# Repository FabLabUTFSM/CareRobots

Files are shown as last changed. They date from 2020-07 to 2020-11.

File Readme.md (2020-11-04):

# CareRobots

<p align="center">
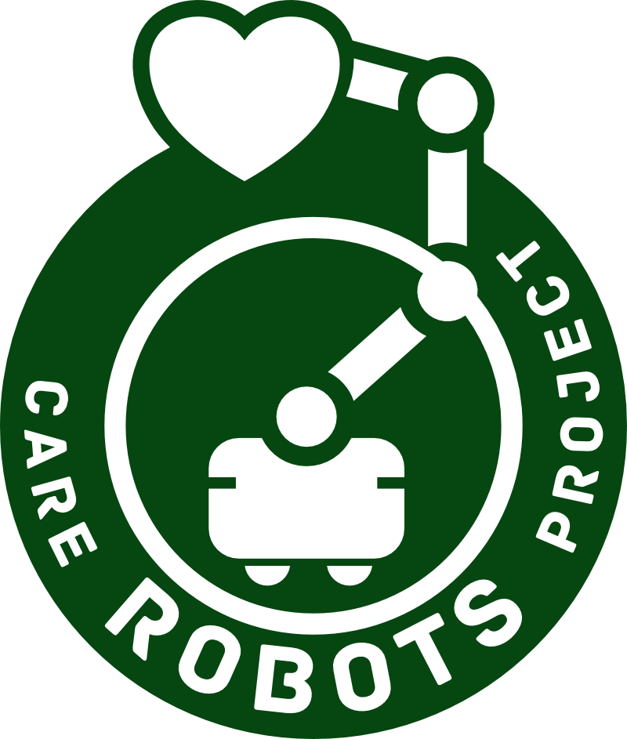
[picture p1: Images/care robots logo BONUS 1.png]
  
</p>

CareRobots is an OpenSoruce project developed by [Fab Lab UTFSM](http://fablab.usm.cl/), [LightHouse-DIG](https://lighthouse-dig.com/), [Center for Engineering Education and Outreach](https://ceeo.tufts.edu/) and [Soko Tech](https://soko.tech/). 

We aim to build low cost telepresence robots, that can be build in any Fab Lab/Makerspace around the world, this robot are intented to protect healthcare service personnel from the COVID-19 spread from infected patients. 

## Firmware

1.0: This firmware is built for an [Adafruit Huzzah feather ESP32](https://learn.adafruit.com/adafruit-huzzah32-esp32-feather/overview), currently other boards aren't working with such reliability.

### Schematic

<p align="center">
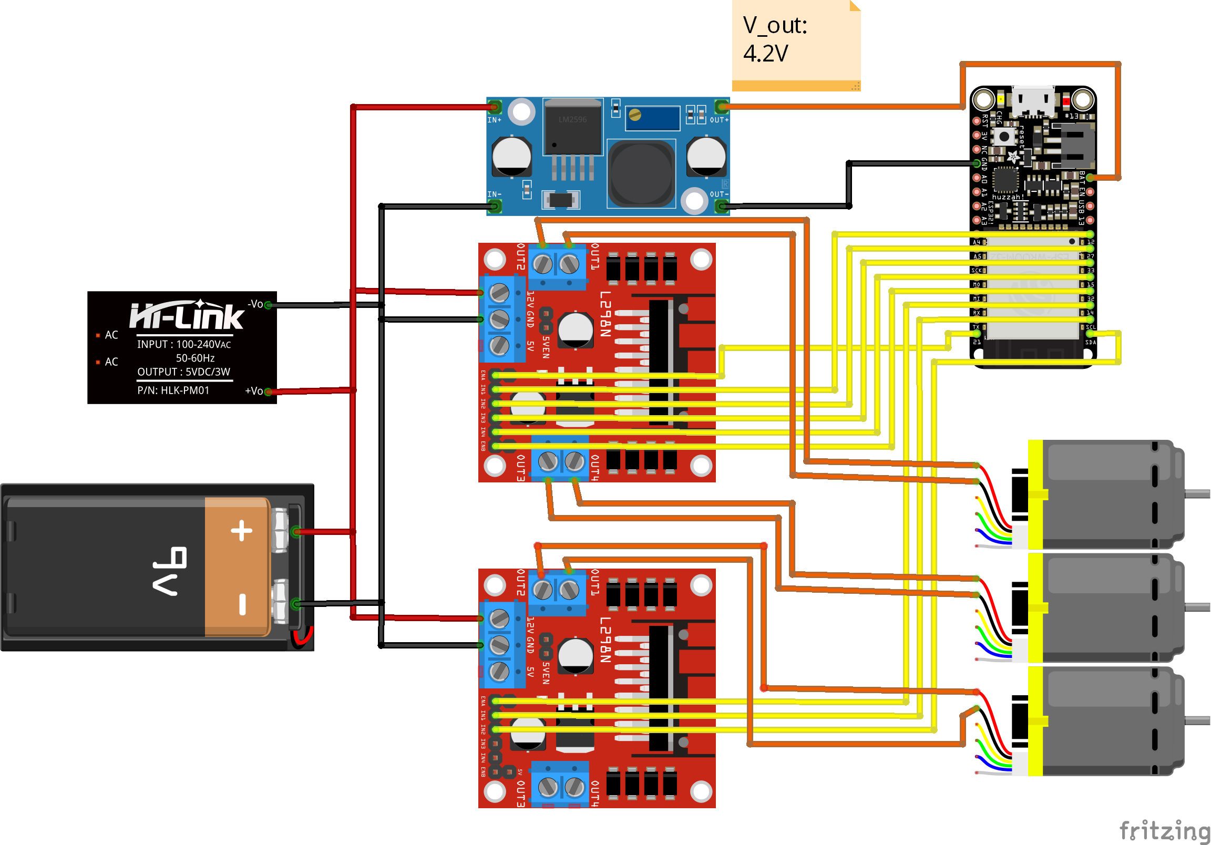
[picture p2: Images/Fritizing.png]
  
</p>

### Libraries

If you are downloading the softwares directlly you hace to coinsider that they are coded using [Platformio](https://platformio.org/), if you are using the Arduino IDE, you will find the codes in the src folder, they will titled as main.cpp (if you fill is more comftable, you can change the extension to .ino), and download the following libraries: 

#### ESP32 - Bluetooth
- [BluetoothSerial](https://github.com/espressif/arduino-esp32/tree/master/libraries/BluetoothSerial)

#### ESP32 - WiFi
- [WebServer](https://github.com/espressif/arduino-esp32/tree/master/libraries/WebServer)
- [analogWrite](https://github.com/ERROPiX/ESP32_AnalogWrite)

#### ESP8266 - WiFi
- [ESP8266WiFi](https://github.com/esp8266/Arduino/tree/master/libraries/ESP8266WiFi)
- [ESP8266WebServer](https://github.com/esp8266/Arduino/tree/master/libraries/ESP8266WebServer)

### Configuration

The current code we have been using is Wifi_ServerClient_ESP32. Key configurations: 

#### WiFi

Set your WiFi passports, to connect the board to your home network.  
```
bool wifiPass = false ; //True if the WiFi network has password; False if not. 
const char* ssid = ""; //WiFi ssid
const char* password = ""; //WiFi password
```

#### Motor Settings

##### Conections

This variables configure the motors pins. In this case, the conection are configured for the conections showed in [Schematic](#Schematic) section. 

```

const int pinMotor[]= {12,27,15,33,22,23};// {moto1CW,motor1CCW,moto2CW,motor2CCW,moto3CW,motor3CCW}
const int pinEnable[]={21,32,14};
const int led = 13;
 ```
##### Torque Ramp Setting

This section works specifically for the torque ramp variables. The torque ramp is used as a patch meanwhile an speed control PID is implemented. 

Key:
* enableTorqueRamp: True if the user is going to work with a torque ramp, false if the user is going to use fix torque value, set in motorSpeed. 
 * maxPayload: PWM payload in wich the robot breaks the inertia. The maximum value it can take is 255. 
 * minPayload: PWM payload for the normal speed we want to aim for our robot. 
 * torqueRampSmoother: Will set te amount of cycles in wich the robot will reach the desired speed. A big number will take more time to reach the speed, but in a smoother way. 
 * delay: Time wich a PWM torque stays working. 
 The ramp time will be defines by the following equation: (maxPayload-minPayload)*delay/toqueRampSmoother. 

```
bool enableTorqueRamp = true;
const int maxPayload = 255;
const int minPayload = 240;
const int torqueRampSmoother =10; 
const int torqueRampDelay= 100; 
const int motorSpeed = 255;
```
##### Motor direction

This variables are designed to control the motor direction from the code and not from the conections. In case a motor is conected in an oposite direction to the shown in the schematics. The user just have to change the variable value for that motor, and it wheel automatically change direction. 

```
bool motor1 = false;
bool motor2 = true;
bool motor3 = false;
```

### Install NodeMCU in Arduino IDE

To install the NodeMCU in the Arduino IDE, you can follow the following [instructions](https://www.instructables.com/id/Quick-Start-to-Nodemcu-ESP8266-on-Arduino-IDE/). 

## Structure

<p align="center">
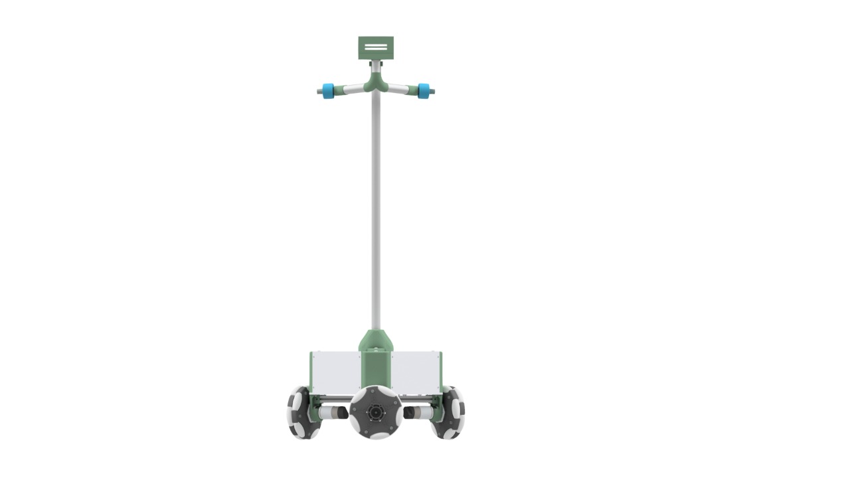
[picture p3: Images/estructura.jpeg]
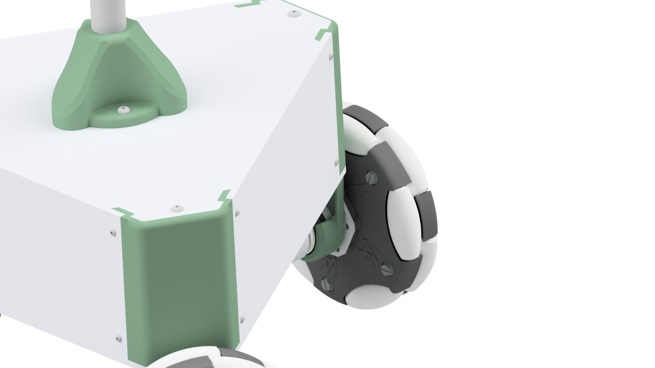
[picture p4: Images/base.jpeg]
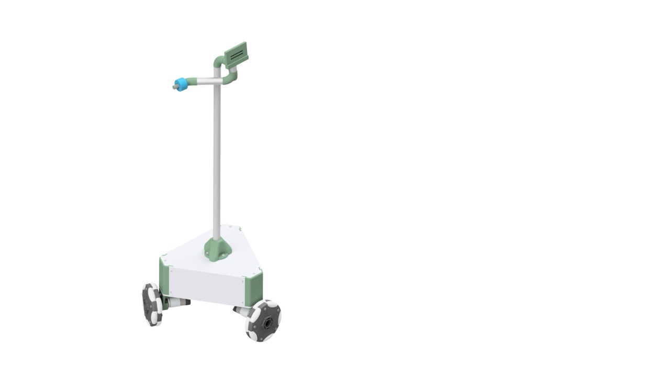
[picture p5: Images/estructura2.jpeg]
   
</p>

## Fabrication 

In order to make CareRobots easy to fabricate in any Fab Lab/Makerspace in the world, we only use 3D printers and laser cutters, all parts can be downloaded in the following [link](https://drive.google.com/drive/folders/1tkrLoz_K_6apnlru4AjxvQd69-fxhUXf?usp=sharing).

### 3D Printed - Structure

|Part Name |Number of parts |  Download Link |
| :-: | :-: |  :-: |
|  B1 | 1  |  [link](https://drive.google.com/file/d/1X95zLryoru4crX6b115vtqp_EDh8kSQb/view?usp=sharing)|
|  B2 | 2  |  [link](https://drive.google.com/file/d/1_fum_8d5C-oLnXPcYOniwOqLqxyNqtJm/view?usp=sharing) |  
|  B3 | 1  |  [link](https://drive.google.com/file/d/1nL7G1LNKwou2jkkLmy965ZC8Md9wTHIw/view?usp=sharing) |
|  Bat | 1  |  [link](https://drive.google.com/file/d/17oT4-NMZ_uCZ2WhJEKf6BcBfo7XZ6th5/view?usp=sharing) |
|  L_v2 | 3  |  [link](https://drive.google.com/file/d/1hJeNZyvru78oPO08zw2eOO0yUmgKt_Df/view?usp=sharing) |
|  M | 3  |  [link](https://drive.google.com/file/d/12ri8eZTseVjtSSoXTZQLDR91Xk1uGaeo/view?usp=sharing) |

### Laser Cutted - Structure

|Part Name |Number of parts | Format |  Download Link |
| :-: | :-: |  :-: | :-: |
| A1  |1 | .dxf |  [link](https://drive.google.com/file/d/1qUMhkHjF6LQkufdu41Rsg2A58V7bNPKg/view?usp=sharing) |
| A1  |1 | .pdf |  [link](https://drive.google.com/file/d/10A2T8DMf_OYUFBTCkRg2jiaPDkv-Y5n-/view?usp=sharing) |
| A2  |1 | .dxf |  [link](https://drive.google.com/file/d/1UI6lDsppqcmhL-nH30FwWpygrrH0wOEs/view?usp=sharing) |
| A2  |1 | .pdf |  [link](https://drive.google.com/file/d/1junfC2UCxdz8u_q4p5oR-OMI-dwqzFFS/view?usp=sharing) |
| A3  |3 | .dxf |  [link](https://drive.google.com/file/d/1FhoujUBVxT0hbg1iW205K-4B8KdyHQ2V/view?usp=sharing) |
| A3  |3 | .pdf |  [link](https://drive.google.com/file/d/18cWZgs_5W19GRg0fgFSUVpIVmK2tZZqf/view?usp=sharing) |

### 3D Printed - Gimbal

__Do not build right away, the structure is being tested in Fab Lab UTFSM, uptdates will be posted__

<p align="center">
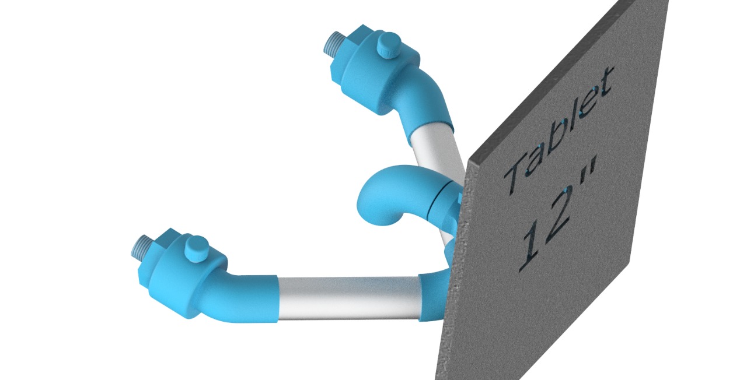
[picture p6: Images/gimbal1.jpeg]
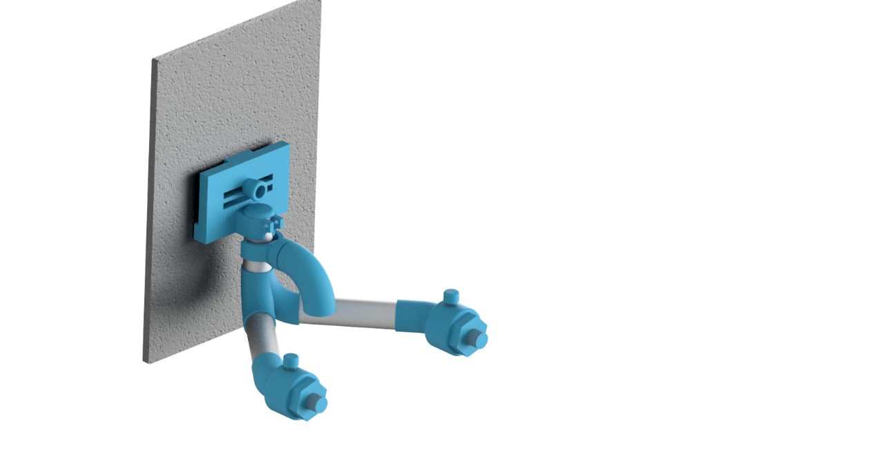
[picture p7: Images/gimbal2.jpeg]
 
</p>

|Part Name |Number of parts | Download Link |
| :-: | :-: |  :-: |
|  100.100.100 Codo Prinicpal | 1  |  [link](https://drive.google.com/file/d/1LrKNzIq5WH4Tc1kQPA7FDwKPdz81MEFJ/view?usp=sharing) |
|  100.100.200 Conector de Pasador | 1  |  [link](https://drive.google.com/file/d/1waasu2H8KbEIScrLwfgzmZHd7Rx-Fj82/view?usp=sharing) |
|  100.200.100 Codo tercero | 1  |  [link](https://drive.google.com/file/d/1nwIYlKD8nJdNT6cQvFXo4gyZvfr2DiPO/view?usp=sharing) |
|  100.200.300 Sujetador | 1  |  [link](https://drive.google.com/file/d/1HpjjEr09sCmCkEBB-0LwTh6nvrJSuSLm/view?usp=sharing) |
|  100.200.400 Codo Secundario  | 1  |  [link](https://drive.google.com/file/d/1zTZWooVP0V9O8LcieDIFtXPp3uPhdiWg/view?usp=sharing) |
|  100.200.500 Peso  | 1  |  [link](https://drive.google.com/file/d/1XWmM778Dlf20GsgeDocvwmgBcEu0HF_q/view?usp=sharing) |
|  100.200.510 Tapa de peso  | 1  |  [link](https://drive.google.com/file/d/1nnNabMoutAxJW8jWdy4tY1yJ_p8wh71P/view?usp=sharing) |
|  100.300.200 Tapa  | 1  |  [link](https://drive.google.com/file/d/1p5FTzZLoxubB07M-G15mzwcnHc5KDI90/view?usp=sharing) |
|  100.400.100 Conector de la tablet  | 1  |  [link](https://drive.google.com/file/d/1OG3XJeAqGO0S7Nu0Kq0IPA0POhfBo3Ik/view?usp=sharing) |
|  100.400.100 Manija | 1  |  [link](https://drive.google.com/file/d/1jl6s8EinCEk0VY1v3JuO_3lAfTZxo3k9/view?usp=sharing) |
|  100.400.400 Soporte Principal | 1  |  [link](https://drive.google.com/file/d/14IcvudmVk-K17IY9RkZWjs_rtM8Tb1c7/view?usp=sharing) |

## Bill of Materials

|Part Name | Quantity | Unit Price  | Download Link |
| :-: | :-: |  :-: | :-: |
| OmniWheel | 3 | $35 |  [link](https://www.andymark.com/products/6-in-duraomni-wheel?sku=am-3154) |
| Motor | 3 | $33 |  [link](https://www.andymark.com/products/neverest-orbital-3-7-gearmotor?sku=am-3461a) |
| Wheel conversion plate | 3 | $5.5 |  [link](https://www.andymark.com/products/wheel-conversion-plate?sku=am-2609a) |
| Motor D-Bore Nub  | 3 | $9 |  [link](https://www.andymark.com/products/6-mm-d-bore-xl-double-boss-nub-w-set-screw?sku=am-3441a) |
| Motor Mount Plate  | 6 | $6 |  [link](https://www.andymark.com/products/picobox-leo-mount-plate?sku=am-3474) |
| NodeMcu | 1 | $4.2 |  [link](https://www.amazon.com/NodeMcu-ESP8266-Internet-Development-Micropython/dp/B07PRMJ6QS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) |
| DC motor driver | 2 | $8.89 |  [link](https://www.amazon.com/-/es/Qunqi-2Packs-Controller-Stepper-Arduino/dp/B01M29YK5U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) |
| 12V 7 amp | 1  | $17.89 |  [link](https://www.amazon.com/ExpertPower-EXP1270-Rechargeable-Lead-Battery/dp/B003S1RQ2S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) |
| DC - DC 5Amp Buck converter | 1  | $6.69 |  [link](https://www.amazon.com/-/es/DZS-Elec-Step-down-Regulator-Converter/dp/B07BDDMGLG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) |
| 12V Battery conector | 1  | $7.99 |  [link](https://www.amazon.com/-/es/KASSupply-Connector-Disconnect-Terminals-Connection/dp/B07M5M8ZCG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) |
| Battery charger | 1  | $10.66 |  [link]( https://www.amazon.com/-/es/Sealed-Lead-Battery-Charger-D1724/dp/B001G8AIMU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 ) |
| Thread M5x250  | 3  | $0.7***|  [link]( https://www.amazon.com/-/es/uxcell-150mm-Stainless-Threaded-Hardware/dp/B01M5DGV0P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) |
| Screw M5x25 | 6  | $0.19* |  [link]( https://www.mcmaster.com/screws/rounded-head-screws/hex-drive-rounded-head-screws/metric-316-stainless-steel-button-head-hex-drive-screws/) |
| Screw M5x16 | 6  | $0.17* |  [link](https://www.mcmaster.com/screws/rounded-head-screws/hex-drive-rounded-head-screws/metric-316-stainless-steel-button-head-hex-drive-screws/ ) |
| Screw M4x16 | 6  | $0.08** |  [link](https://www.mcmaster.com/screws/rounded-head-screws/hex-drive-rounded-head-screws/metric-316-stainless-steel-button-head-hex-drive-screws/ ) |
| Screw M3x16 | 38  | $0.05** |  [link](https://www.mcmaster.com/screws/rounded-head-screws/hex-drive-rounded-head-screws/metric-316-stainless-steel-button-head-hex-drive-screws/ ) |
| M5 nut | 24  | $0.06** |  [link](https://www.mcmaster.com/nuts/hex-nuts/metric-18-8-stainless-steel-hex-nuts/ ) |
| M4 nut | 3  | $0.06** |  [link](https://www.mcmaster.com/nuts/hex-nuts/metric-18-8-stainless-steel-hex-nuts/ ) |
| M3 nut | -  | $0.06** |  [link](https://www.mcmaster.com/nuts/hex-nuts/metric-18-8-stainless-steel-hex-nuts/ ) |
| M3 Set Screw | 6  | $0.1* |  [link](https://www.mcmaster.com/nuts/hex-nuts/metric-18-8-stainless-steel-hex-nuts/ ) |

*50 unit package
**100 unit package
***10 unit package

## Assembly

Pictures of the assembly process. 

## To do

- Add external antenna [link](https://randomnerdtutorials.com/esp32-cam-connect-external-antenna/)
- Add charge battery [link](https://www.amazon.com/Charging-Control-Module-Controller-Lithium-ion/dp/B07P83BPTR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)
- Unify code for ESP8266 and ESP32 
- Identify why non Adafruit boards doesn't work.

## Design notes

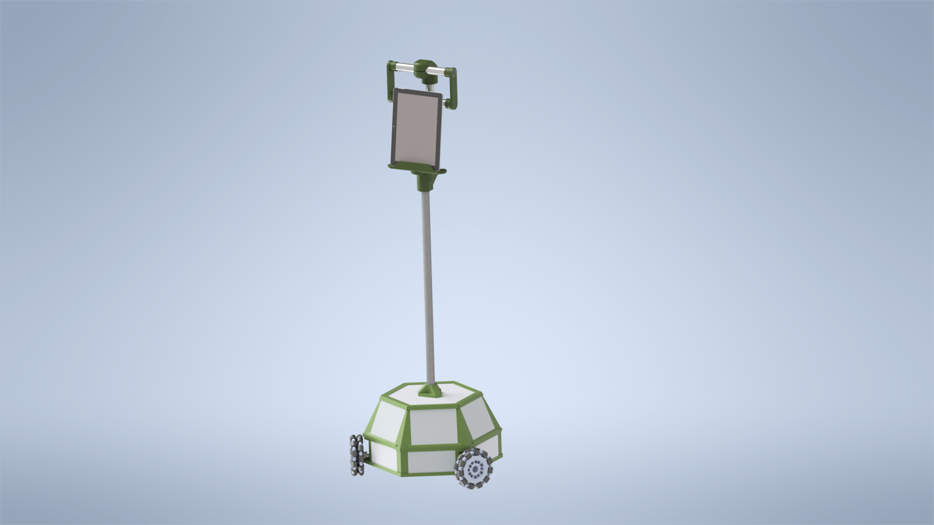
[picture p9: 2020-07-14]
Images/CareRobot.png

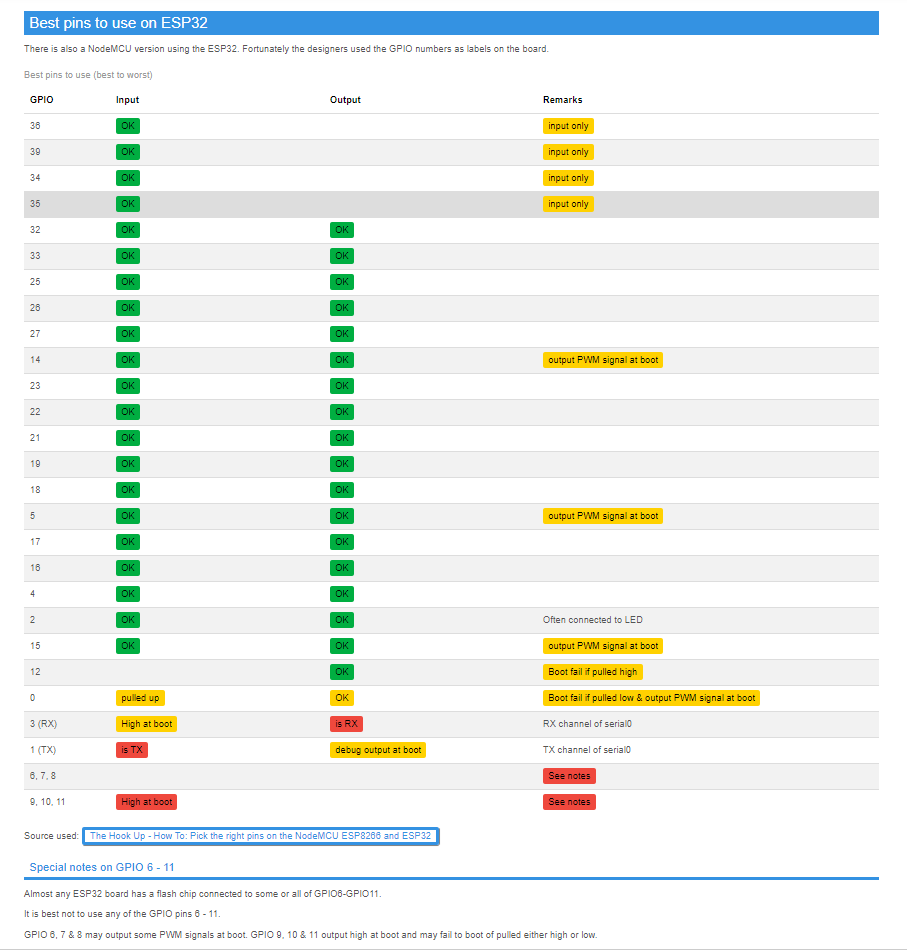
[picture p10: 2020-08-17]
Images/esp32Pins.PNG

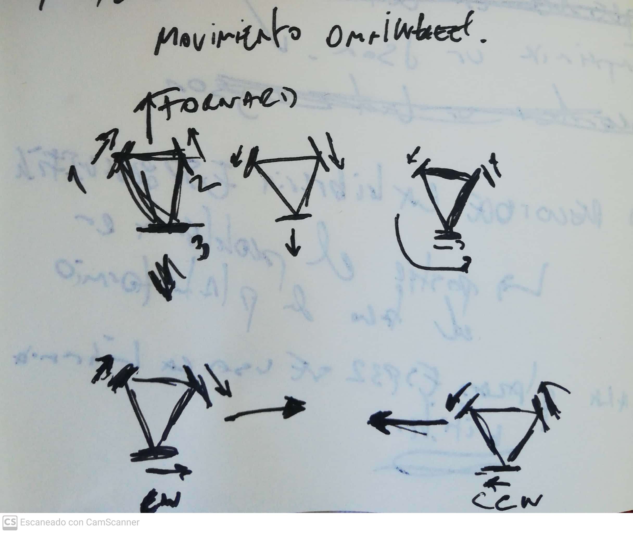
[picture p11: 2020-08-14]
Images/Omniwheel.jpg

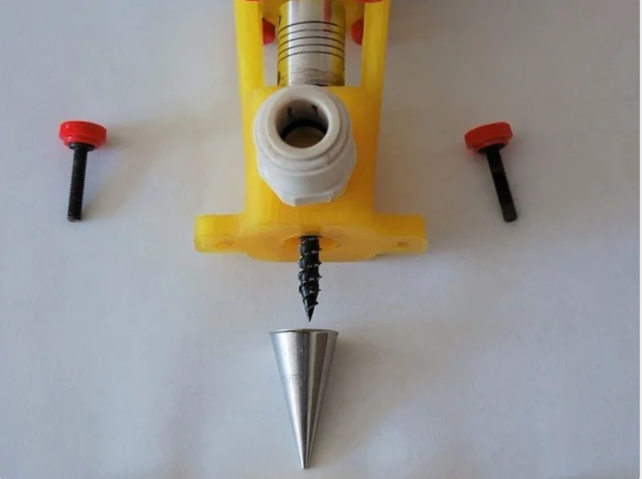
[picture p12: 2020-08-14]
Images/documentacion2.png

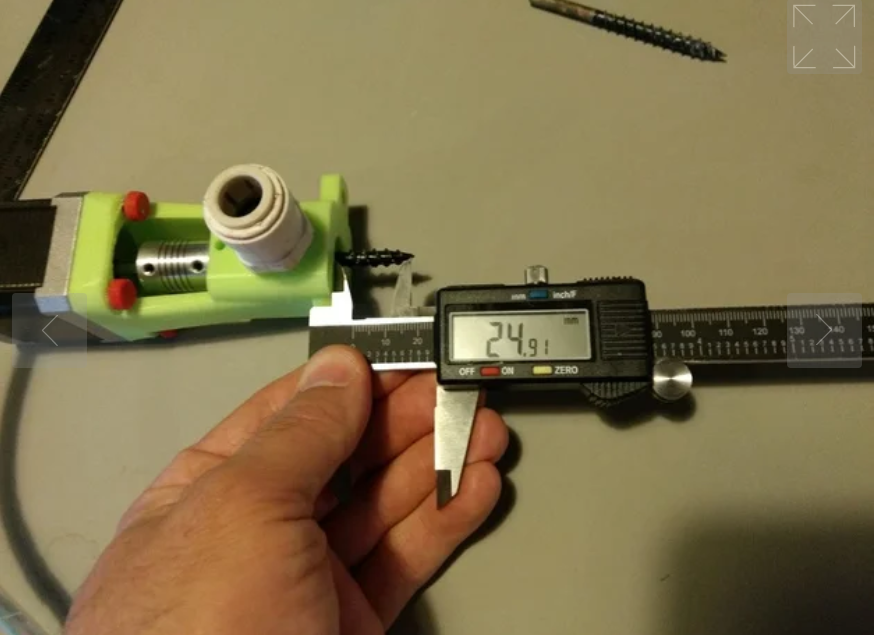
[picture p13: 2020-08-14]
Images/documentacion3.png

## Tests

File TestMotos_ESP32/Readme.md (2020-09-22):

# Motor test

This code has been programed to test the motors conections. 

Once it is uploaded to the board, the motors shouls move ClockWise, stop with a delay of one second and then move Counterclockwise, making the robot spin around its axis. 

In case the robot moves in any other direction rather than spinning, it means that a motor has been conected in a wrong way and its moving in an oposite direction than the other ones. 

To change this go to: 

```
bool motor1 = true;
bool motor2 = true;
bool motor3 = true;
```
This boolean variables define the motor spinning direction, changing this value will change it. 

In case that the motor doesn't move, check the motor conection pins in the line: 

```
const int pinMotor[]= {12,27,15,33,22,23};// {moto1CW,motor1CCW,moto2CW,motor2CCW,moto3CW,motor3CCW}
const int pinEnable[]={13,32,14};
```

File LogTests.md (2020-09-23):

Pendientes (23/09): 

- Añadir boton ON/OFF para el robot
- Añadir boton de reset 
- Cerra Gimbal
- Probar contrapeso
- Enchufe de carga bateria
- Circuito carga bateria ([5](https://github.com/FabLabUTFSM/CareRobots/issues/5))

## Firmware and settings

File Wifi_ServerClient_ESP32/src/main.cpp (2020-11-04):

/***********CONFIGURATION************
 * This section will define all the variables the user is spected to
 * configurate, please don't modify the other sections*/

bool wifiPass = false ; //True if the WiFi network has password; False if not. 
const char* ssid = "MIT"; //WiFi ssid
const char* password = ""; //WiFi password

/*******CONECTIONS: Modify the next 2 lines to define the pins your are going to use. 
 * Dont modifiy nothing of you are using the same conections presented in the Fritzing 
 * image. */

const int pinMotor[]= {12,27,15,33,22,23};// {moto1CW,motor1CCW,moto2CW,motor2CCW,moto3CW,motor3CCW}
const int pinEnable[]={13,32,14};
const int led = 21;

 
/*******************TORQUE RAMP CONFIGURATION*********/
/**Key:
 * maxPayload: PWM payload in wich the robot breaks the inertia. The maximum value it can take is 255.  
 * minPayload: PWM payload for the normal speed we want to aim for our robot. 
 * torqueRampSmoother: Will set te amount of cycles in wich the robot will reach the desired speed. A big number will take more time to reach the speed, but in a smoother way. 
 * delay: Time wich a PWM torque stays working. 
 The ramp time will be defines by the following equation: (maxPayload-minPayload)*delay/toqueRampSmoother. 
*************************************************************************************************/
bool enableTorqueRamp = false; // True uses torqueRamo as RPM variable, false uses motorSpeed. 
const int maxPayload = 255;
const int minPayload = 100;
const int torqueRampSmoother =10; //The smaller this number is, the slower the acceleration will be. 
const int torqueRampDelay= 500; 
const int motorSpeed = 255; //Motor speed, this variable will define the motor speed, to define the number follow the following ecuation: Max_RPM*motorSpeed/255=Speed_expected. 

/*****************MOTOR DIRECTION**********/
bool motor1 = false;
bool motor2 = true;
bool motor3 = false;

/******DON NOT MODIFY PASS HERE*********/

#include <WiFi.h>
#include <WebServer.h>
#include "analogWrite.h"
#include "ESPAsyncWebServer.h"

AsyncWebServer server(80); 


bool inMove = false;

/****Unused variables
const int motorSpeed = 140; //Motor speed, this variable will define the motor speed, to define the number follow the following ecuation: Max_RPM*motorSpeed/255=Speed_expected. 
bool motorTimeControl = true; //True if the users wants to control the time the robot is activated, false if not. 
const int motorDelay = 100; //Defines the amount of time the robot will move 
*///


/// Create the website
String getPage(){
  //String page = "<html lang=fr-FR><head><meta http-equiv='refresh' content='10'/>";
  String page = "<html lang=fr-FR><head>";
  page += "<title>COVID19-CareROBOT v1.0</title>";
  page += "<style> body { background-color: #fffff; font-family: Arial, Helvetica, Sans-Serif; Color: #000088; }</style>";
  page += "</head><body><h1>COVID19-CareBOT v1.0</h1>";
  page += "<table>";
  page += " <tr> ";
  page += "   <th></th> ";
  page += "   <th><form action=\"/UP\" method=\"POST\"><input type=\"submit\" value=\"&#x2B06;\"></form></th>";
  page += "   <th></th>" ;
  page += " </tr>" ;
  page += " <tr>" ;
  page += "  <td><form action=\"/LEFT\" method=\"POST\"><input type=\"submit\" value=\"&#x2B05;\"></form></td>" ;
  page += "   <td><form action=\"/STOP\" method=\"POST\"><input type=\"submit\" value=\"&#x25FC;\"></form></td>" ;
  page += "   <td><form action=\"/RIGHT\" method=\"POST\"><input type=\"submit\" value=\"&#x27A1;\"></form></td>" ;
  page += " </tr>" ;
  page += " <tr>" ;
  page += "   <td></td>" ;
  page += "   <td><form action=\"/DOWN\" method=\"POST\"><input type=\"submit\" value=\"&#x2B07;\"></form></td>" ;
  page += "   <td></td>" ;
  page += " </tr>" ;
  page += " <tr>" ;
  page += "   <td></td>" ;
  page += "   <td><form action=\"/CW\" method=\"POST\"><input type=\"submit\" value=\"&#x21BB;\"></form></td>" ;
  page += "   <td><form action=\"/CCW\" method=\"POST\"><input type=\"submit\" value=\"&#x21ba;\"></form></td>";
  page += "   <td></td>" ;         
  page += " </tr>" ;
  page += " </table>" ;
  page += "</body></html>";
  return page;
}


//Function declaration

String handleRoot();
String handleUp();
String handleDown();
String handleLeft();
String handleRight();
String handleCW();
String handleCCW();
String handleStop();
void moveMotor(int motor, String direction); 
void forward();
void left();
void right();
void left();
void down();
void CCW();
void CW();
void stop();
void torqueRamp(String motor1Status, String motor2Status, String motor3Status);

//http variables
String up_send="dont move";
String down_send="dont move";
String left_send="dont move";
String right_send="dont move";
String cw_send="dont move";
String ccw_send="dont move";
String stop_send="move";

void setup(void){
  pinMode(led,OUTPUT);
  digitalWrite(led,LOW);
  for (byte i=0; i< sizeof(pinMotor); i++ ){
    pinMode(pinMotor[i],OUTPUT);
    digitalWrite(pinMotor[i],LOW);
  }
  for (byte i=0; i< sizeof(pinEnable); i++ ){
    pinMode(pinEnable[i],OUTPUT);
    digitalWrite(pinMotor[i],LOW);
  }
  Serial.begin(115200);         // Start the Serial communication to send messages to the computer
  delay(10);
  Serial.println('\n');

  //connect to your local wi-fi network, Uncomment if the wifi has password or not. 
  if (wifiPass){
    WiFi.begin(ssid,password);
  }
  else
  {
    WiFi.begin(ssid);
  } 

  //check wi-fi is connected to wi-fi network
  while (WiFi.status() != WL_CONNECTED) {
    delay(1000);
    Serial.print(".");
  }
  digitalWrite(led,HIGH);
  Serial.println("");
  Serial.println("WiFi connected..!");
  Serial.print("Got IP: "); 
  Serial.println(WiFi.localIP());
  String page = getPage();

  server.on("/", HTTP_GET, [](AsyncWebServerRequest *request){
    request->send_P(200, "text/html", handleRoot().c_str());
  });
    server.on("/UP", HTTP_POST, [](AsyncWebServerRequest *request){
    up_send="move";
    forward();
    Serial.println("forward"); 
    request->redirect("/");
  });
  server.on("/UP_Client", HTTP_GET, [](AsyncWebServerRequest *request){
    request->send_P(200, "text/html", handleUp().c_str());
  });
  server.on("/DOWN", HTTP_POST, [](AsyncWebServerRequest *request){
    down_send="move";
    down();
    Serial.println("down"); 
    request->redirect("/");
  });
    server.on("/DOWN_Client", HTTP_GET, [](AsyncWebServerRequest *request){
    request->send_P(200, "text/html", handleDown().c_str());
  });
  server.on("/LEFT", HTTP_POST, [](AsyncWebServerRequest *request){
    left_send="move";
    left();
    Serial.println("left");
    request->redirect("/");
  });
  server.on("/LEFT_Client", HTTP_GET, [](AsyncWebServerRequest *request){
    request->send_P(200, "text/html", handleLeft().c_str());
  });
  server.on("/RIGHT", HTTP_POST, [](AsyncWebServerRequest *request){
    right_send="move";
    right();
    Serial.println("right");
    request->redirect("/");
  });
  server.on("/RIGHT_Client", HTTP_GET, [](AsyncWebServerRequest *request){
    request->send_P(200, "text/html", handleRight().c_str());
  });
  server.on("/CW", HTTP_POST, [](AsyncWebServerRequest *request){
    cw_send="move";
    CW();
    Serial.println("CW");
    request->redirect("/");
  });
  server.on("/CW_Client", HTTP_GET, [](AsyncWebServerRequest *request){
    request->send_P(200, "text/html", handleCW().c_str());
  });
  server.on("/CCW", HTTP_POST, [](AsyncWebServerRequest *request){
    ccw_send="move";
    CCW();
    Serial.println("CCW");
    request->redirect("/");
  });
    server.on("/CCW_Client", HTTP_GET, [](AsyncWebServerRequest *request){
    request->send_P(200, "text/html", handleCCW().c_str());
  });
  server.on("/STOP", HTTP_POST, [](AsyncWebServerRequest *request){
    stop_send="dont move";
    stop();
    Serial.println("stop");
    request->redirect("/");
  });
    server.on("/STOP_Client", HTTP_GET, [](AsyncWebServerRequest *request){
    request->send_P(200, "text/html", handleStop().c_str());
  });

  server.begin();                           // Actually start the server
  Serial.println("HTTP server started");

}

void loop(){
   if (WiFi.status() == WL_CONNECTED){
     digitalWrite(led,HIGH);
   }
   else
   {
     digitalWrite(led,LOW);
   }
      
    
}

String handleRoot() {
  return getPage();
}

String handleUp(){
  String input=up_send;
  up_send= "dont move";
  return input;
}

String handleDown(){
  String input=down_send;
  down_send= "dont move"; 
  return input;
}
String handleLeft(){
  String input=left_send;
  left_send= "dont move"; 
  return input;
}

String handleRight(){
  String input=right_send;
  right_send= "dont move"; 
  return input;
}

String handleCW(){
  String input=cw_send;
  cw_send= "dont move"; 
  return input;
}

String handleCCW(){
  String input=ccw_send;
  ccw_send= "dont move"; 
  return input;
}

String handleStop(){
  String input=stop_send;
  stop_send= "move"; 
  return input;
}

//Standar functions for bluetooth and WiFi
void forward(){
  moveMotor(1,"CCW");
  moveMotor(2,"CW");
  moveMotor(3,"Off");
  if (enableTorqueRamp)
  {
    torqueRamp("CCW","CW","Off");
  }
}

void left(){
  moveMotor(1,"CCW");
  moveMotor(2,"CCW");
  moveMotor(3,"CW");
  if (enableTorqueRamp)
  {
    torqueRamp("CCW","CCW","CW");
  }
}

void right(){
  moveMotor(1,"CW");
  moveMotor(2,"CW");
  moveMotor(3,"CCW");
  if (enableTorqueRamp){
    torqueRamp("CW","CW","CCW");
  }
}

void down(){
  moveMotor(1,"CW");
  moveMotor(2,"CCW");
  moveMotor(3,"Off");
  if (enableTorqueRamp)
  {
    torqueRamp("CW","CCW","Off");
  }
}

void stop(){
  moveMotor(1,"Off");
  moveMotor(2,"Off");
  moveMotor(3,"Off");
  inMove=false;
}

void CW(){
  moveMotor(1,"CW");
  moveMotor(2,"CW");
  moveMotor(3,"CW");
  if (enableTorqueRamp){
    torqueRamp("CW","CW","CW");
  }
}

void CCW(){
  moveMotor(1,"CCW");
  moveMotor(2,"CCW");
  moveMotor(3,"CCW");
  if (enableTorqueRamp){
    torqueRamp("CCW","CCW","CCW");
  }
}


void moveMotor(int motor, String direction){
  switch (motor){
    case 1:
      if (!enableTorqueRamp){
        analogWrite(pinEnable[0],motorSpeed);
      }
      if(direction == "CCW"){
        if (motor1){
          digitalWrite(pinMotor[0],LOW);
          digitalWrite(pinMotor[1],HIGH);
        }
        else
        {
          digitalWrite(pinMotor[0],HIGH);
          digitalWrite(pinMotor[1],LOW);
        }
        
        Serial.print("Motor1: ");
        Serial.println("CCW");
      }
      else if (direction=="CW")
      {
        if (motor1){
          digitalWrite(pinMotor[0],HIGH);
          digitalWrite(pinMotor[1],LOW);
        }
        else
        {
          digitalWrite(pinMotor[0],LOW);
          digitalWrite(pinMotor[1],HIGH);
        }
        Serial.print("Motor1: ");
        Serial.println("CW");
      }
      else 
      {
        digitalWrite(pinEnable[0],LOW);
        digitalWrite(pinMotor[0],LOW);
        digitalWrite(pinMotor[1],LOW);
        Serial.print("Motor1: ");
        Serial.println("Off");
      }
      break;
    case 2:
      if (!enableTorqueRamp){ 
        analogWrite(pinEnable[1],motorSpeed);
      }
      if(direction == "CCW"){
        if (motor2){
          digitalWrite(pinMotor[2],LOW);
          digitalWrite(pinMotor[3],HIGH);
        }
        else
        {
          digitalWrite(pinMotor[2],HIGH);
          digitalWrite(pinMotor[3],LOW);
        }
        Serial.print("Motor2: ");
        Serial.println("CCW");
      }
      else if (direction=="CW")
      {
        if (motor2)
        {
          digitalWrite(pinMotor[2],HIGH);
          digitalWrite(pinMotor[3],LOW);
        }
        else
        {
          digitalWrite(pinMotor[2],LOW);
          digitalWrite(pinMotor[3],HIGH);
        }
        
        Serial.print("Motor2: ");
        Serial.println("CW");
      }
      else 
      {   
        digitalWrite(pinEnable[1],LOW);
        digitalWrite(pinMotor[2],LOW);
        digitalWrite(pinMotor[3],LOW);
        Serial.print("Motor2: ");
        Serial.println("Off");
      }
      break;
    case 3:
      if (!enableTorqueRamp){
        analogWrite(pinEnable[2],motorSpeed);
      }
      if(direction == "CCW"){
        if (motor3){
          digitalWrite(pinMotor[4],LOW);
          digitalWrite(pinMotor[5],HIGH);
        }
        else
        {
          digitalWrite(pinMotor[4],HIGH);
          digitalWrite(pinMotor[5],LOW);
        }
        Serial.print("Motor3: ");
        Serial.println("CCW");
      }
      else if (direction=="CW")
      {
        if (motor3)
        {
          digitalWrite(pinMotor[4],HIGH);
          digitalWrite(pinMotor[5],LOW);
        }
        else
        {
          digitalWrite(pinMotor[4],LOW);
          digitalWrite(pinMotor[5],HIGH);
        }
        Serial.print("Motor3: ");
        Serial.println("CW");
      }
      else 
      {
        analogWrite(pinEnable[2],LOW);
        digitalWrite(pinMotor[4],LOW);
        digitalWrite(pinMotor[5],LOW);
        Serial.print("Motor3: ");
        Serial.println("Off");
      }
      break;
  }
}

void torqueRamp(String motor1Status, String motor2Status, String motor3Status){
  int payload = maxPayload;
  int delta = (maxPayload-minPayload)/torqueRampSmoother;
  if(!inMove){
    Serial.println("Torque Ramp");
    while (payload > minPayload)
    {
      if (motor1Status != "Off")
      {
        analogWrite(pinEnable[0],payload);
      }
      if (motor2Status != "Off")
      {
        analogWrite(pinEnable[1],payload);
      }
      if (motor3Status != "Off")
      {
        analogWrite(pinEnable[2],payload);
      }
      payload=payload-delta;
      delay(torqueRampDelay);
    }
    inMove= true;
  }
}

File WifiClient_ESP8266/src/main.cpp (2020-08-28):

  
#include <ESP8266WiFi.h>
#include <ESP8266HTTPClient.h>
#include <WiFiClient.h>

const char* ssid = "MIT";
const char* password = "lololo111";

const char* serverNameUp = "http://18.21.85.70/UP_Client";
const char* serverNameDown = "http://18.21.85.70/DOWN_Client";
const char* serverNameLeft = "http://18.21.85.70/LEFT_Client";
const char* serverNameRight = "http://18.21.85.70/RIGHT_Client";
const char* serverNameCW = "http://18.21.85.70/CW_Client";
const char* serverNameCCW = "http://18.21.85.70/CCW_Client";
const char* serverNameStop = "http://18.21.85.70/STOP_Client";


String httpGETRequest(const char* server);
void moveMotor(int motor, String direction);  /// Function that makes the motor rotate CW or CCW --> Joseto
void forward();
void left();
void right();
void left();
void down();
void CCW();
void CW();
void scan();
void stop();

const int pinMotor[]= {5,16,2,0,13,15};// {moto1CW,motor1CCW,moto2CW,motor2CCW,moto3CW,motor3CCW}

const int pinEnable[]={4,14,12};

const int motorSpeed = 10;

void setup() {
Serial.begin(115200);
//WiFi.begin(ssid,password);
WiFi.begin(ssid);
while(WiFi.status() != WL_CONNECTED) { 
    delay(500);
    Serial.print(".");
}
Serial.println("");
Serial.print("Connected to WiFi network with IP Address: ");
Serial.println(WiFi.localIP());
moveMotor(1,"Off");
moveMotor(2,"Off");
moveMotor(3,"Off");
ESP.wdtDisable();
ESP.wdtEnable(WDTO_8S);

}

void loop() {
  scan();
  ESP.wdtFeed();
}

void scan(){
  String upStatus = httpGETRequest(serverNameUp);
  if(upStatus=="move"){
    forward();
    Serial.println("forward");
  }
  String downStatus = httpGETRequest(serverNameDown);
  if(downStatus=="move"){
    down();
    Serial.println("down");
  }
  String leftStatus = httpGETRequest(serverNameLeft);
  if(leftStatus=="move"){
    left();
    Serial.println("left");
  }
  String rightStatus = httpGETRequest(serverNameRight);
  if(rightStatus=="move"){
    right();
    Serial.println("right");
  }
  String cwStatus = httpGETRequest(serverNameCW);
  if(cwStatus=="move"){
    CW();
    Serial.println("cw");
  }
  String ccwStatus = httpGETRequest(serverNameCCW);
  if(ccwStatus=="move"){
    CCW();
    Serial.println("ccw");
  }
  String stopStatus = httpGETRequest(serverNameStop);
  if(stopStatus=="dont move"){
    stop();
    Serial.println("stop");
  }
}

String httpGETRequest(const char* server) {
  HTTPClient http;
  WiFiClient client;
    
  // Your IP address with path or Domain name with URL path 
  http.begin(client,server);
  
  // Send HTTP POST request
  int httpResponseCode = http.GET();
  
  String payload = "--"; 
  
  if (httpResponseCode>0) {
    //Serial.println(httpResponseCode);
    payload = http.getString();
  }
  else {
  }
  // Free resources
  http.end();

  return payload;
}

//Standar functions for bluetooth and WiFi
void forward(){
  moveMotor(1,"CCW");
  moveMotor(2,"Off");
  moveMotor(3,"Off");
}

void left(){
  moveMotor(1,"Off");
  moveMotor(2,"CW");
  moveMotor(3,"Off");

}

void right(){
  moveMotor(1,"Off");
  moveMotor(2,"Off");
  moveMotor(3,"CCW");
}

void down(){
  moveMotor(1,"CW");
  moveMotor(2,"CCW");
  moveMotor(3,"Off");
}

void stop(){
  moveMotor(1,"Off");
  moveMotor(2,"Off");
  moveMotor(3,"Off");
}

void CW(){
  moveMotor(1,"CW");
  moveMotor(2,"CW");
  moveMotor(3,"CW");
}

void CCW(){
  moveMotor(1,"CCW");
  moveMotor(2,"CCW");
  moveMotor(3,"CCW");
}


void moveMotor(int motor, String direction){
  switch (motor){
    case 1:
      analogWrite(pinEnable[0],motorSpeed);
      if(direction == "CCW"){
        digitalWrite(pinMotor[0],LOW);
        digitalWrite(pinMotor[1],HIGH);
        //Serial.print("Motor1: ");
        //Serial.println("CCW");
      }
      else if (direction=="CW")
      {
        digitalWrite(pinMotor[0],HIGH);
        digitalWrite(pinMotor[1],LOW);
        //Serial.print("Motor1: ");
        //Serial.println("CW");
      }
      else 
      {
        digitalWrite(pinEnable[0],LOW);
        digitalWrite(pinMotor[0],LOW);
        digitalWrite(pinMotor[1],LOW);
        //Serial.print("Motor1: ");
        //Serial.println("Off");
      }
      break;
    case 2: 
      analogWrite(pinEnable[1],motorSpeed);
      if(direction == "CCW"){
        digitalWrite(pinMotor[2],LOW);
        digitalWrite(pinMotor[3],HIGH);
        //Serial.print("Motor2: ");
        //Serial.println("CCW");
      }
      else if (direction=="CW")
      {
        digitalWrite(pinMotor[2],HIGH);
        digitalWrite(pinMotor[3],LOW);
        //Serial.print("Motor2: ");
        //Serial.println("CW");
      }
      else 
      {   
        digitalWrite(pinEnable[1],LOW);
        digitalWrite(pinMotor[2],LOW);
        digitalWrite(pinMotor[3],LOW);
        //Serial.print("Motor2: ");
        //Serial.println("Off");
      }
      break;
    case 3:
      analogWrite(pinEnable[2],motorSpeed);
      if(direction == "CCW"){
        digitalWrite(pinMotor[4],LOW);
        digitalWrite(pinMotor[5],HIGH);
        //Serial.print("Motor3: ");
        //Serial.println("CCW");
      }
      else if (direction=="CW")
      {
        digitalWrite(pinMotor[4],HIGH);
        digitalWrite(pinMotor[5],LOW);
        //Serial.print("Motor3: ");
        //Serial.println("CW");
      }
      else 
      {
        digitalWrite(pinEnable[1],LOW);
        digitalWrite(pinMotor[4],LOW);
        digitalWrite(pinMotor[5],LOW);
        //Serial.print("Motor3: ");
        //Serial.println("Off");
      }
      break;
  }

}

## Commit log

2020-07-18 BOM Update
2020-07-31 read a json from ArduinoJson
2020-08-05 protocolos de comunicacion
2020-08-11 comandos para wifi en ESP32 listos
2020-08-19 last stable version - the PWM doesn't work
2020-08-20 change platformio config for china board
2020-08-28 New branch as master
    [CurrentConection_wifi-ESP32.fzz, FritzingSketch.fzz]
2020-09-21 Add code ESP32 client server
2020-09-21 add variables to change motor direction
2020-09-22 add code test motors
2020-09-22 Add readme to MotorTest
2020-09-22 add PWM function to regulate motor speed in WiFi ServerClient
2020-09-23 Add torque ramp function to WiFiServerClient_ESP32 and WiFiClient_ESP32 and deleted WiFiClientESP32 because it was doubled
2020-09-30 Test motors
2020-10-29 edit Fritzing, first modifications to Wifi_ClientServe_ESP32 after test1
    [FritzingSketch.fzz]
2020-10-30 eliminate motor vibration, set pins as low. Include LED to check boards conection
    [FritzingSketch.fzz]
